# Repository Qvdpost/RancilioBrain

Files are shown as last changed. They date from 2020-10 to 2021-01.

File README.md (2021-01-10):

# RancilioBrain
##### This is a work in progress

## Interface Parts
InstallationRender
partStack

You certainly dont need to puchase these components from amazon, you can find them on ebay or banggood or aliexpress as well. It's usually worth it to get a few of the same because it's easy to ruin them during prototyping. 

1 [5.08mm Pitch Screw Terminals](https://www.amazon.com/gp/product/B07DQNVLL8/ref=ppx_yo_dt_b_search_asin_title?ie=UTF8&psc=1)
2 [128 x 64 OLED](https://www.amazon.com/gp/product/B085WCRS7C/ref=ppx_yo_dt_b_search_asin_title?ie=UTF8&psc=1)
4 [Perf Board](https://www.amazon.com/Solderable-BreadBoard-matches-breadboards-1-85in/dp/B00LLO4Q7W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)
5 [120v AC to 5v DC](https://www.amazon.com/gp/product/B07YXN8J6R/ref=ppx_yo_dt_b_search_asin_title?ie=UTF8&psc=1)
6 [Large Aluminum Knob](https://www.amazon.com/gp/product/B087M2QCC2/ref=ppx_yo_dt_b_search_asin_title?ie=UTF8&psc=1)
7 [Rotary Encoder](https://www.amazon.com/gp/product/B07DM2YMT4/ref=ppx_yo_dt_b_search_asin_title?ie=UTF8&psc=1)
8 [Arduino Nano](https://www.amazon.com/gp/product/B07KCH534K/ref=ppx_yo_dt_b_search_asin_title?ie=UTF8&psc=1)
11 [2.54mm Pitch Screw Terminals](https://www.amazon.com/gp/product/B07NSJV6NW/ref=ppx_yo_dt_b_search_asin_title?ie=UTF8&psc=1)

## Other Parts
SSRs

Besides the enclosure assembly, you will need suitable wire, various [spade connectors](https://www.amazon.com/gp/product/B078PMWNJC/ref=ppx_yo_dt_b_search_asin_title?ie=UTF8&psc=1) and 2 quality [40A Relays](https://www.amazon.com/gp/product/B00E1LC1VK/ref=ppx_yo_dt_b_search_asin_title?ie=UTF8&psc=1). I've used 200ºC Temp resistant silicone wire for all lengths runnning inside the machine, [18AWG](https://www.amazon.com/gp/product/B0746HMTPP/ref=ppx_yo_dt_b_search_asin_title?ie=UTF8&psc=1) for the relays and [22AWG](https://www.amazon.com/gp/product/B01M0O1NXM/ref=ppx_yo_dt_b_search_asin_title?ie=UTF8&psc=1) for the 5V signal wires.

## Circuitry
wiring diagram

You will also need to reroute the ground to the 3 way valve so that solenoid if you plan to have solenoid control independent of pump control like I do. Otherwise just piggyback the poles of the brew switch.

board-cad

A wiring scheme for the Arduino and other parts.

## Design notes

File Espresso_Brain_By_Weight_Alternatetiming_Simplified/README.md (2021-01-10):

# RancilioBrain Simplified

This version of the project only contains a single load cell and a single relais. For some machines you can piggyback the wiring on the brew switch so that can save you a relay. 

If you can get a design working that accurately weighs with only one load cell, and can piggyback the brew switch, this is the source code you'll want to load onto your Arduino.

NOTE: Currently the code for this project is not up to date with the regular project!

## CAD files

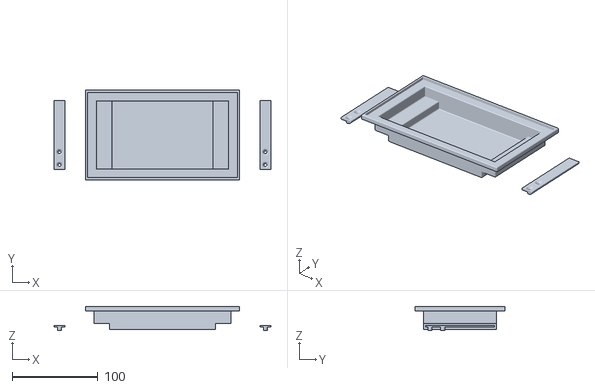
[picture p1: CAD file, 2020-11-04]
3D_Printables_WIP(NOT_Perfect)/QuickMillDripTrayShortAndSupports.stl
253.0 x 105.0 x 28.0

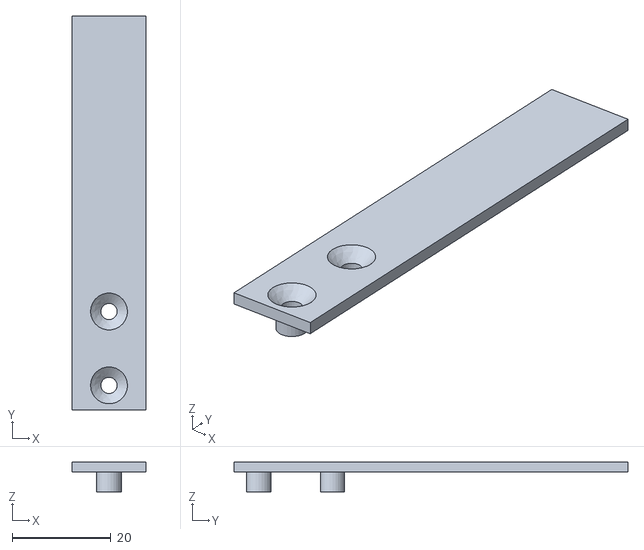
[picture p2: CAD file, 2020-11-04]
3D_Printables_WIP(NOT_Perfect)/QuickMillSupport.stl
15.0 x 80.0 x 6.00

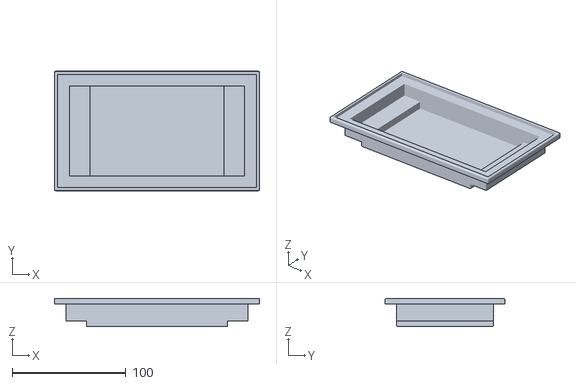
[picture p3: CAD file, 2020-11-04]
3D_Printables_WIP(NOT_Perfect)/QuickMillDripTrayShort.stl
180.0 x 105.0 x 25.0

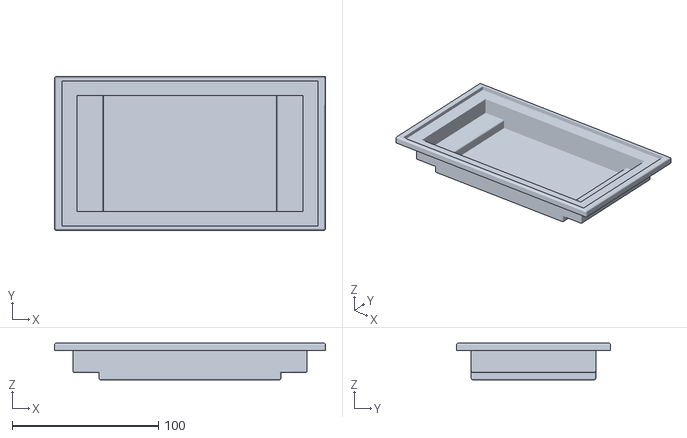
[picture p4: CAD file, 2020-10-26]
3D_Printables_WIP(NOT_Perfect)/QuickMillDripTray.stl
185.0 x 105.0 x 25.0

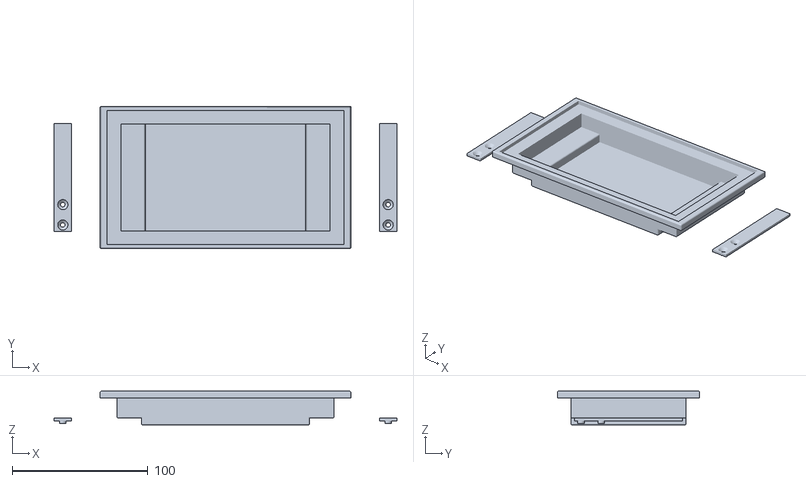
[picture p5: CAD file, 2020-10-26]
3D_Printables_WIP(NOT_Perfect)/QuickMillDripTrayAndSupports.stl
253.0 x 105.0 x 25.0

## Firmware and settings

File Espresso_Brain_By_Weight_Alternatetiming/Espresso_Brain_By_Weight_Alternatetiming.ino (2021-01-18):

// OLED control library
#include <Adafruit_SSD1306.h>

// Arduino flash memory control library
// This is being used to store the target weight so when arduino power cycles it retains last used weight
#include <EEPROM.h>

// this is the little board that comes with each load cell
// URL: https://github.com/RobTillaart/HX711
#include "HX711.h"


// OLED-screen setup
#define SCREEN_WIDTH 128
#define SCREEN_HEIGHT 64
// Reset pin # (or -1 if sharing Arduino reset pin)
#define OLED_RESET     4
Adafruit_SSD1306 display(SCREEN_WIDTH, SCREEN_HEIGHT, &Wire, OLED_RESET);

// Scale setup
HX711 scale;
HX711 scale2;
uint8_t dataPin = 5;
uint8_t clockPin = 6;
uint8_t dataPin2 = 11;
uint8_t clockPin2 = 12;
// This is the calibration value for each load cell, you need to calibrate
// them with a known weight The good thing is that the value is linear so if
// you know something weights 100g you can calculate what the value should be.
#define scaleCalibration 2040.54
#define scaleCalibration2 1986.60



// the variable to hold a value for each load cell (float because it is a decimal)
float w1;
float w2;

// Weight control variables
int currentWeight;
int lastWeight;
bool weightReached = false;
int targetWeight;
int weightOffset = 0; // This value is how many decigrams before the target should the pump shut off, you need to test


/*
   Macros and globals needed for the offset hashtable based on flowrate
*/
// The interval over which the flow is calculated
#define flowTime 4
// Maximum flowrate to remember offset for, in centigrams per second
#define maxFlow 500
// Flow rate bucketsize in centigrams per second
#define flowInterval 20
// starting postion in EEPROM to write the offset hashtable
#define hashOffset 10
// Delta in offsets to warrant a new write to EEPROM in centigrams
#define offsetPrecision 50

int hashMax = maxFlow / flowInterval;
int hashStep = flowInterval;
int weightFlow[flowTime] = {0};

// Flow of coffee measured as centigram per flowTime - 1
int currentFlow;
int lastFlow;



// Timing control variables
const unsigned long eventInterval = 100;
const unsigned long reachedInterval = 5000; // DEPRECATED: (will be changed into flowrate) how long to keep reading and updating the weight after the target weight is reached in milliseconds
unsigned long previousTime = 0;
unsigned long startCounting;
unsigned long currentTime;
unsigned int currentSecond = 0;
// NOTE: tV is interchangeable with elapsedTime; why do both exist?
unsigned long elapsedTime;
unsigned long tV = 0;

// This is the weight that arduino will default to when powered on
int storedWeight;


// This is rudimentary state logic
bool started = false;
bool preStarted = false;


// The rotary encoder
int buttonPin = 4;
int buttonPinState = 1;
int buttonPinLast = 1;
bool buttonPressed = 0;
int pinA = 2;
int pinB = 3;
int pinAStateCurrent = HIGH;
int pinAStateLast = pinAStateCurrent;
bool turnDetected = false;


// The Relays
int pump = 9;
int valve = 10;

// Helper functions that turn the relays on and off
void extractOn() {
  digitalWrite(pump, HIGH);
  digitalWrite(valve, HIGH);
}

void extractOff() {
  digitalWrite(pump, LOW);
  digitalWrite(valve, LOW);
}



/***
   These are the different layouts for each screen that we will use,
   helps keep our code more readable to break them out like this
 ***/

/*
   When you first turn the machine on
*/
void preStartedDisplay() {
  display.setTextSize(1);
  display.setTextColor(SSD1306_WHITE); // Draw white text
  display.setCursor(0, 0);
  display.print("Target Weight");
  display.setTextSize(2);
  display.setTextColor(SSD1306_WHITE); // Draw white text
  display.setCursor(0, 14);
  display.print(targetWeight * 0.01, 1);
  display.print(" g");


  // if you've pulled a shot already put the info on screen (if TV isnt 0 you've pulled a shot)
  if (tV != 0) {
    display.setTextSize(1); // this is size..  1 is 8 pixels tall, 2 is 16, and so on
    display.setTextColor(SSD1306_WHITE); // Draw white text
    display.setCursor(0, 32); // this is position in (x,y)
    display.print("Prev Weight"); //display.print sends this to buffer
    display.setTextSize(1);
    display.setTextColor(SSD1306_WHITE); // Draw white text
    display.setCursor(82, 32);
    display.print(lastWeight * 0.01, 1);
    display.print(" g");
    display.setTextSize(1); 
    display.setTextColor(SSD1306_WHITE); // Draw white text
    display.setCursor(0, 44); 
    display.print("Prev Flow"); 
    display.setTextSize(1);
    display.setTextColor(SSD1306_WHITE); // Draw white text
    display.setCursor(82, 44);
    display.print(lastFlow * 0.01, 1);
    display.print(" g/s");
    display.setTextSize(1);
    display.setTextColor(SSD1306_WHITE); // Draw white text
    display.setCursor(0, 56);
    display.print("Prev Time");
    display.setTextSize(1);
    display.setTextColor(SSD1306_WHITE); // Draw white text
    display.setCursor(82, 56);
    display.print(tV / 1000.0, 1);
    display.print(" s");
  }
}

/*
   When the shot is being pulled this is what is shown
*/
void startedDisplay() {

  display.setTextSize(1);
  display.setTextColor(SSD1306_WHITE); // Draw white text
  display.setCursor(0, 0);
  display.print("Target Weight");
  display.setTextSize(1);
  display.setTextColor(SSD1306_WHITE); // Draw white text
  display.setCursor(85, 0);
  display.print(targetWeight * 0.01, 1);
  display.print(" g");
  display.setTextSize(2);
  display.setTextColor(SSD1306_WHITE); // Draw white text
  display.setCursor(0, 22);
  display.print("Weight");
  display.setTextSize(1);
  display.setTextColor(SSD1306_WHITE); // Draw white text
  display.setCursor(80, 22);
  display.print(currentWeight * 0.01, 1);
  display.print(" g");
  display.setTextSize(1);
  display.setTextColor(SSD1306_WHITE); // Draw white text
  display.setCursor(80, 34);
  display.print(currentFlow * 0.01, 1);
  display.print(" g/s");
  display.setTextSize(2);
  display.setTextColor(SSD1306_WHITE); // Draw white text
  display.setCursor(0, 46);
  display.print("Time");
  display.setTextSize(2);
  display.setTextColor(SSD1306_WHITE); // Draw white text
  display.setCursor(80, 46);
  display.print(tV / 1000.0, 1);
  display.print(" s");
}

/*
   This is identical to when a shot is pulled only we switch to a more precise method of reading the scale (called lastWeight)
   NOTE: This can be merged somehow with startedDisplay()
*/
void justEndedDisplay() {
  display.setTextSize(1);
  display.setTextColor(SSD1306_WHITE); // Draw white text
  display.setCursor(0, 0);
  display.print("Target Weight");
  display.setTextSize(1);
  display.setTextColor(SSD1306_WHITE); // Draw white text
  display.setCursor(85, 0);
  display.print(targetWeight * 0.01, 1);
  display.print(" g");
  display.setTextSize(2);
  display.setTextColor(SSD1306_WHITE); // Draw white text
  display.setCursor(0, 22);
  display.print("Weight");
  display.setTextSize(1);
  display.setTextColor(SSD1306_WHITE); // Draw white text
  display.setCursor(80, 22);
  display.print(lastWeight * 0.01, 1);
  display.print(" g");
  display.setTextSize(1);
  display.setTextColor(SSD1306_WHITE); // Draw white text
  display.setCursor(80, 34);
  display.print(lastFlow * 0.01, 1);
  display.print(" g/s");
  display.setTextSize(2);
  display.setTextColor(SSD1306_WHITE); // Draw white text
  display.setCursor(0, 46);
  display.print("Time");
  display.setTextSize(2);
  display.setTextColor(SSD1306_WHITE); // Draw white text
  display.setCursor(80, 46);
  display.print(tV / 1000.0, 1);
  display.print(" s");

}


/*
   This is just that text "starting" that appears after you click the encoder but before the pump is on.
*/
void startingDisplay() {
  display.clearDisplay();
  display.setTextSize(2);
  display.setTextColor(SSD1306_WHITE); // Draw white text
  display.setCursor(15, 18);
  display.print("Starting");
  display.display();
}


/*
   This function adds or subtracts .1 to the target weight if you turn left or right
*/
void increment() {
  // NOTE: What is this for? Does not seem to be used anywhere.
  turnDetected = true;

  // Rotation
  pinAStateCurrent = digitalRead(pinA);
  if ((pinAStateLast == LOW) && (pinAStateCurrent == HIGH)) {
    if (digitalRead(pinB) == HIGH) {
      targetWeight -= 100;
      delay(15);
    } else {
      targetWeight += 100;
      delay(15);
    }
  }
  pinAStateLast = pinAStateCurrent;
}

/*
   This function checks to see if the button was pressed
*/
void buttonDetect() {
  buttonPinState = digitalRead(buttonPin);

  if (buttonPinState != buttonPinLast) {
    // Extraction just started
    if ((buttonPinState == 1) && (!started)) {
      preStarted = false;
      startingDisplay();
      tareScales();
      delay(250);
      tV = 0;
      currentWeight = 0;
      lastFlow = 0;
      elapsedTime = 0;
      preStarted = false;
      started = true;
      extractOn();
      startCounting = millis();
      display.clearDisplay();
    }

    // Manual stop on extraction
    if ((elapsedTime > 1.0) && (buttonPinState == 1) && (started)) {
      weightReached = true;
    }
    buttonPinLast = buttonPinState;
  }
}


/*
   This is the interupt that we create in our setup, the conditional statement means if you rotate the encoder
   while a shot is extracting it wont run any code and cause lag
*/
void update() {
  if (preStarted) {
    increment();
  }
}

// --------------//--------------//--------------//--------------//--------------//--------------//--------------//--------------//--------------
// --------------//--------------//--------------//--------------//--------------//--------------//--------------//--------------//--------------

void setup() {
  Serial.begin(9600);

  // display setup
  if (!display.begin(SSD1306_SWITCHCAPVCC, 0x3C)) { // Address 0x3C for 128x32
    Serial.println(F("SSD1306 allocation failed"));
    for (;;); // Don't proceed, loop forever

  }

  // This is seeing if this is the first time you are writing to the eeprom and if it is just put a 0 for now
  if (EEPROM.read(256) != 123) {
    EEPROM.write(256, 123);
    storedWeight = 0;
  }

  // This code runs every time the arduino powers back on... it sets the target weight to the last weight used so that it "remembers"
  else {
    EEPROM.get(0, storedWeight);
  }

  targetWeight = storedWeight;

  // setting up the relays
  pinMode(pump, OUTPUT);
  pinMode(valve, OUTPUT);

  // making sure the pump and valve are off, probably dont need but just in case
  extractOff();

  // initial display
  display.clearDisplay();
  preStartedDisplay();
  display.display();

  // This is our rotary encoder setup
  pinMode(buttonPin, INPUT_PULLUP); // initialize the button pin as a input
  pinMode(pinA, INPUT_PULLUP);
  pinMode(pinB, INPUT_PULLUP);
  attachInterrupt(digitalPinToInterrupt(pinA), update, CHANGE);


  // This initializes the scales
  scale.begin(dataPin, clockPin);
  scale2.begin(dataPin2, clockPin2);

  // Calibrate to initially weighted value
  scale.set_scale(scaleCalibration);
  scale2.set_scale(scaleCalibration2);

  // set the scales to 0
  scale.tare();
  scale2.tare();

  // Set the state of the system
  preStarted = true;
}

// --------------//--------------//--------------//--------------//--------------//--------------//--------------//--------------//--------------//--------------
// --------------//--------------//--------------//--------------//--------------//--------------//--------------//--------------//--------------//--------------

void loop() {

  // check to see if extraction is running and perform a get weight if it is
  if ((preStarted == false) && (!weightReached)) {
    scaleFunc();
  }
  // check to see if the shot just ended and switch to doing multiple averaged readings for more accuracy
  else if ((preStarted == false) && (weightReached)) {
    precisionScale();
  }

  currentTime = millis();

  // check if button is pressed and run the button detect code we defined earlier
  buttonDetect();

  // Updates the time and weight value while the extraction is happening
  if (started) {
    updateWeightFlow();
    
    // this is to only start counting extraction time from the first drips into the cup
    if (currentWeight < 1) {
      startCounting = currentTime;
    }
    
    if (!weightReached) {
      elapsedTime = currentTime - startCounting;
      tV = elapsedTime;
      previousTime = currentTime;
      display.clearDisplay();
      startedDisplay();
      display.display();
    }
  }

  // This is the code to stop the extraction once the target weight is reached.
  // I added the conditional to only runs 5s after extraction starts because
  // sometimes you need to reposition your cup and that would trip
  // the weight and stop extraction and ruin your shot :(

  if (tV > 2000) {
    readWeightOffset();
    if ((currentWeight) > (targetWeight - weightOffset)) {
      lastWeight = currentWeight;
      if (lastFlow == 0) {
        lastFlow = currentFlow;
      }
      weightReached = true;
      if (storedWeight != targetWeight) {
        storedWeight = targetWeight;
        EEPROM.put(0, storedWeight);
      }
    }
  }

  // Updates the weight for a few more moments just after the shot has stopped extracting and timer has stopped
  if (weightReached && started) {
    extractOff();
    display.clearDisplay();
    justEndedDisplay();
    display.display();
    if (currentWeight > lastWeight) {
      lastWeight = currentWeight;
    }
  }

  /* this code runs after your weight is reached AND a certain extra
     amount of time has passed, you know for the last few drips...
  */
  if (weightReached && currentFlow < 10) {
    started = 0;
    weightReached = false;
    preStarted = true;
    writeWeightOffset();
    clearWeightFlow();
    currentWeight = 0;
  }

  // Goes back to the initial standby screen when you are finished extracting so you can set another weight
  if (!started) {
    display.clearDisplay();
    preStartedDisplay();
    display.display();
  }

}

// --------------//--------------//--------------//--------------//--------------//--------------//--------------//--------------//--------------//--------------
// --------------//--------------//--------------//--------------//--------------//--------------//--------------//--------------//--------------//--------------

/***
   A few helper functions
*/

/*
   This asks the scales to get the weight and add them up
*/
void scaleFunc() {
  w1 = scale.get_units() + 0.6;
  w2 = scale2.get_units();
  if ((w1 + w2) > 1) {
    currentWeight = round((w1 * 100 + w2 * 100));
  }
}

/*
   This asks the scales to check the weight twice so in theory its more accurate, this is how the shot is weighed just after the pump is off
*/
void precisionScale() {
  w1 = scale.get_units(2) + 0.6;
  w2 = scale2.get_units(2);
  currentWeight = round((w1 * 100 + w2 * 100));
}

/*
   We tare the cells just after the rotary knob is clicked
*/
void tareScales() {
  scale.tare();
  scale2.tare();
}

/*
   Keeps track of the last N seconds of weights and recalculateds the flow
*/
void updateWeightFlow() {
  if (currentTime / 1000 != currentSecond) {
    currentSecond = currentTime / 1000;
    weightFlow[currentSecond % flowTime] = currentWeight;
    calcCurrentWeightFlow();
  }
}

/*
   Clears the weightFlow array for a new extraction
*/
void clearWeightFlow() {
  for (int i = 0; i < flowTime; i++) {
    weightFlow[i] = 0;
  }
}

/*
   Returns the flow over an interval of N seconds (measurements taken at the start of each second)
*/
void calcCurrentWeightFlow() {
  int minVal = weightFlow[0];
  int maxVal = weightFlow[0];

  for (int i = 1; i < flowTime; i++) {
    minVal = min(minVal, weightFlow[i]);
    maxVal = max(maxVal, weightFlow[i]);
  }

  // Average weight difference over interval flowTime
  // (e.g. when flowTime is 2 you have measured 1 second of weight difference)
  currentFlow = (maxVal - minVal) / (flowTime - 1);
}

/*
   Calculates an index in EEPROM memory based on the current flowrate
*/
uint8_t hashFlow() {
  uint8_t hash = (currentFlow / hashStep);
  return (hash < hashMax ? hash : hashMax) + hashOffset;
}

/*
   Calculates an index in EEPROM memory based on the last flowrate during extraction
*/
uint8_t hashLastFlow() {
  uint8_t hash = (lastFlow / hashStep);
  return (hash < hashMax ? hash : hashMax) + hashOffset;
}

/*
   Reads the weightOffset from EEPROM memory related to the current flowrate
*/
void readWeightOffset() {
  int offset = EEPROM.read(hashFlow());
  // Convert offset from decigrams to centigrams
  weightOffset = offset != 255 ? offset * 10 : 0;
}

/*
   Writes the final weight overflow (drip) to EEPROM memory based on the flowrate
   before target weight was reached
*/
void writeWeightOffset() {
  uint8_t offset = EEPROM.read(hashLastFlow());
  int currentOffset = currentWeight - targetWeight;

  /* The final weight was less than the weight during extraction (e.g. someone took away the cup)
     Or the overflow too great (e.g. someone leaned on the scale)
  */
  if (currentWeight < lastWeight - offsetPrecision || currentOffset > 1.5 * targetWeight) {
    return;
  }

  int deltaOffset = currentOffset - offset;

  // Write the offset to EEPROM in decigrams
  if (abs(deltaOffset) > offsetPrecision) {
    // Convert offset to decigrams
    currentOffset = currentOffset / 10;

    // 255 is reserved for unset values so 254 is chosen if the value is 255 or higher due to EEPROM limitations
    currentOffset = currentOffset < 255 ? currentOffset : 254;

    // new offset is the sum of old plus new (negative if stopped too early)
    currentOffset = max(0, offset + currentOffset);
    
    EEPROM.write(hashLastFlow(), currentOffset);
  }
}

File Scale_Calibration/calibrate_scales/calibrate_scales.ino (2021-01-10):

//
//    FILE: HX_kitchen_scale.ino
//  AUTHOR: Rob Tillaart
// VERSION: 0.1.0
// PURPOSE: HX711 demo
//     URL: https://github.com/RobTillaart/HX711
//
// HISTORY:
// 0.1.0    2020-06-16 initial version
//

#include "HX711.h"

HX711 scale;

uint8_t dataPin = 5;
uint8_t clockPin = 6;

float callibration_weight = 139;


void setup()
{
  Serial.begin(9600);

  scale.begin(dataPin, clockPin);

  scale.set_scale(1000);

  Serial.print("UNITS: ");
  Serial.println(scale.get_units());
  
  Serial.println("\nEmpty the scale, press a key to continue");
  while(!Serial.available());
  while(Serial.available()) Serial.read();
  
  scale.tare();
  Serial.print("UNITS: ");
  Serial.println(scale.get_units());


  Serial.print("\nPut ");
  Serial.print(callibration_weight);
  Serial.println(" grams on the scale, then press a key to continue");
  while(!Serial.available());
  while(Serial.available()) Serial.read();

  scale.callibrate_scale(callibration_weight);
  Serial.print("UNITS: ");
  Serial.println(scale.get_units(10));

  Serial.println("\nScale is callibrated, press a key to continue");
  while(!Serial.available());
  while(Serial.available()) Serial.read();

}

void loop()
{
  Serial.print("UNITS: ");
  Serial.print(scale.get_units());
  Serial.print("\tSCALE: ");
  Serial.print(scale.get_scale());
  Serial.print("\tOFFSET: ");
  Serial.println(scale.get_offset());
  delay(250);
}

// END OF FILE

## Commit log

2020-10-26 Quick Mill stl files and code updates
    [QuickMillDripTrayAndSupports.stl]
2020-10-26 exported all objects this time
    [QuickMillDripTrayAndSupports.stl]
2020-10-26 rounder edges
    [QuickMillDripTrayAndSupports.stl]
2020-10-26 shortened tray and seperated stls
    [QuickMillDripTray.stl, QuickMillDripTrayShort.stl, QuickMillSupport.stl]
2020-11-04 simplified brain and updated stls
    [QuickMillDripTrayShort.stl, QuickMillDripTrayShortAndSupports.stl, QuickMillSupport.stl]
2021-01-10 readmes and flowrate display
2021-01-11 fixed bug in writing offset & changed flowtime window
    [Espresso_Brain_By_Weight_Alternatetiming.ino]
